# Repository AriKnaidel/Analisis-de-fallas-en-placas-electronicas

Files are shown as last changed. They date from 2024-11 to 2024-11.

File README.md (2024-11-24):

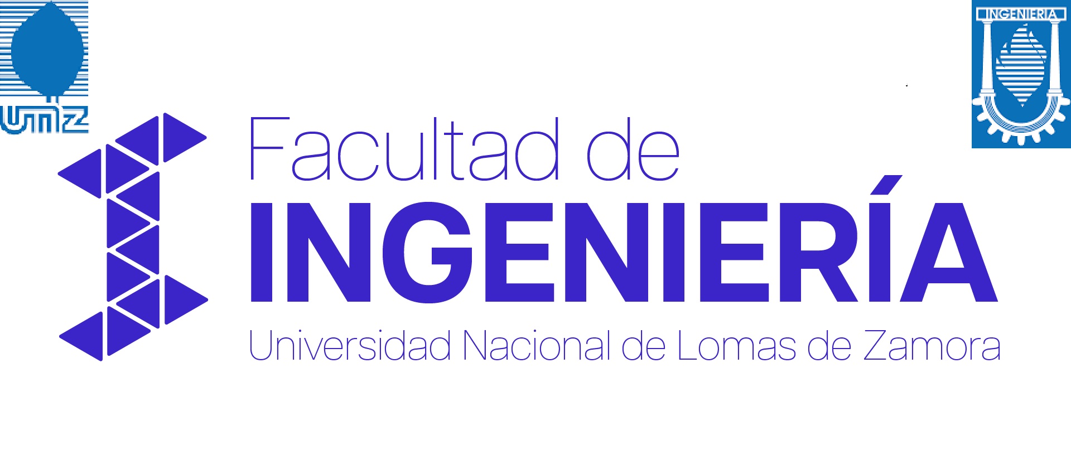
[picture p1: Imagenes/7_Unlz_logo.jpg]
Descripción de la imagen


<h1 align="center">Análisis de fallas en placas electrónicas</h1>

# Detalle del trabajo realizado

El trabajo que realicé es un dispositivo mecatrónico que inspecciona placas electrónicas mediante una cámara y un robot, para luego informar las fallas detectadas. Está pensado para recibir placas electrónicas al final de una línea de producción y verificar que las mismas cuenten con las necesidades mínimas para ser aprobadas, controlando tanto los diferentes elementos electrónicos como los errores de soldadura mediante una cámara y realizando mediciones sobre la placa a través de un robot SCARA. El resultado de estos tres análisis es el que corroborará si placa está o no en condiciones para pasar dicho control de calidad. Todo esto será controlado a través de una interfaz gráfica desarrollada en Python, donde también se podrá observar en tiempo real las diferentes detecciones y mediciones realizadas sobre la placa. 

# Elementos Móviles
El prototipo está formado por tres elementos móviles, y si bien todos se controlan mediante placas electrónicas tipo Arduino estos elementos están integrados mediante un programa de Python para que coordinen sus movimientos y analicen las diferentes placas. Estos elementos son: un robot de tipo SCARA, la base porta placa y un elevador.
# Robot SCARA
El robot SCARA diseñado íntegramente en SOLIDWORKS e impreso con impresora 3D, es de tres grados de libertad (dos giros y un desplazamiento lineal). Este será el encardo de realizar los movimientos necesarios para posicionarse en los puntos de testeo de las placas, y gracias a su efector (puntas de medición) tomará las mediciones correspondientes. Medirá continuidad entre los puntos de testeo de la placa, y se tomarán como válidas las placas que presenten continuidad sobre esos puntos. 

Dicho robot está formado por tres mecanismos móviles (la base, el brazo, regulación de altura) y cada uno cuenta con un motor paso a paso nema 17 que es el encargado de darle el movimiento a cada mecanismo. La base es giratoria y está formada por dos rodamientos axiales de 60mm de diámetro exterior, los cuales acoplan mediante tornillos y tuercas a una polea dentada de 60 dientes, dicha polea acopla a otra polea de 20 dientes a 150mm de distancia ubicada en el eje del motor mediante una correa dentada gt2 de 400mm. De esta base salen tres varillas lisas de 6mm de diámetro y también una varilla roscada de 8mm de diámetro, es en estas varillas donde se acopla el mecanismo del brazo, el cual contiene al brazo 1, al brazo 2 y al efector, este último se encuentra al final del brazo 2. Dicho mecanismo está acoplado a las varillas lisas mediante rodamientos lineales de 6mm de diámetro y a la varilla roscada mediante una tuerca, por lo tanto, este mecanismo gira en concordancia con la base ya que está montado sobre ella. Y como también esta acoplado al mecanismo de regulación de altura cuando la varilla roscada gira, hace que este mecanismo se eleve o baje. El acople entre el motor nema 17 y el brazo 2 es exactamente igual al de la base. En el caso del mecanismo de regulación de altura, el eje del motor está directamente acoplado, mediante un acople flexible a dicha varilla roscada, esta es de 8 mm por vuelta, por lo tanto, cuando este motor gira una vuelta hace que el mecanismo del brazo se eleve o baje 8mm.

Para controlar el robot SCARA se diseñó una placa electrónica mediante el software PROTEUS, luego ese diseño fue impreso en una hoja transfer para transferir las pistas a la placa de cobre y posteriormente se utilizó cloruro férrico para eliminar el cobre y obtener el diseño útil sobre la placa. A dicha placa se le acoplo una esp32, 3 drivers A4988, y borneras para utilizar los pines como entradas o salidas de la esp32. 

<p align="center">
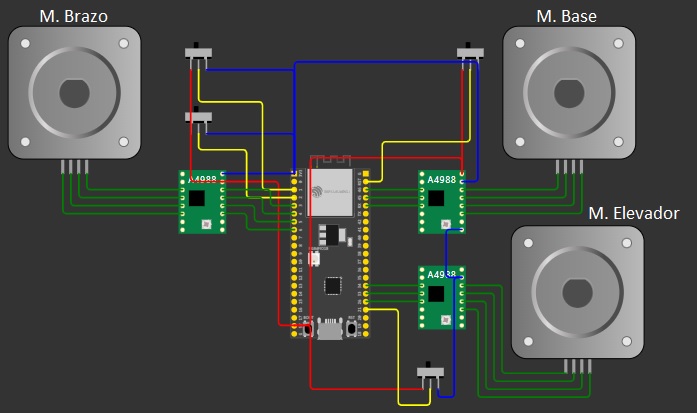
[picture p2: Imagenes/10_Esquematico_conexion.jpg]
Descripción de la imagen
  
</p>
<p align="center"><em>Esquematico conexion robot</em></p>

La esp32 es la encargada de controlar el robot SCARA, esta contiene el código desarrollado en el Arduino IDE, y es capaz de realizar todos los cálculos de la cinemática inversa para que los motores giren la cantidad de grados necesarios y se posicionen en las ubicaciones correctas realizando todos los movimientos al mismo tiempo. Ejecuta la rutina de Home antes de cada movimiento de medición en la placa. Realiza las mediciones de continuidad en dicha placa, gracias al efector del robot. Y también sensa los finales de carrera presentes en el robot para evitar colisiones.

<table>
  <tr>
    <td style="text-align: center;">
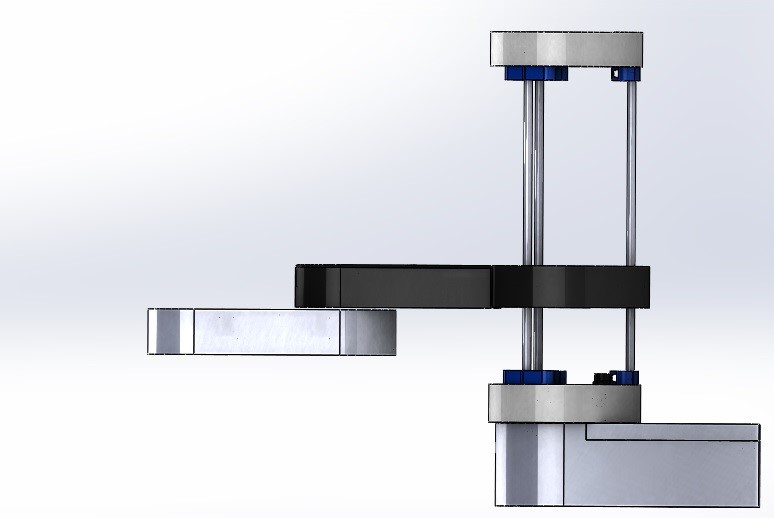
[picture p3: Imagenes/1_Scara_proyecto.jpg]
Descripción de la imagen 1
      
      <p style="text-align: center;"><em>Robot SCARA</em></p>
    </td>
    <td style="text-align: center;">
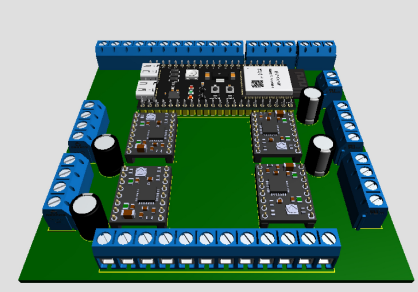
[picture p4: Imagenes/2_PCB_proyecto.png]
Descripción de la imagen 2
      
      <p style="text-align: center;"><em>Controlador Robot SCARA</em></p>
    </td>
  </tr>
</table>

# Cinemática inversa
Con la cinemática inversa, a partir de las coordenadas (x,y) se obtienen los ángulos Ɵ1 y Ɵ2, luego esos ángulos se traducen a pasos para que los motores realicen su trabajo. En el caso del eje que varía la altura se trata de manera separada, es decir no es incluido en los cálculos de cinemática inversa, ya que para el caso de robots de tipo SCARA no es necesario. 

<p align="center">
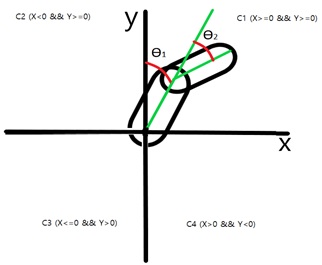
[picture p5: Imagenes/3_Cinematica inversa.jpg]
Descripción de la imagen
  
</p>
<p align="center"><em>Cinemática inversa</em></p>

Para el cálculo de los ángulos Ɵ1 y Ɵ2 se utilizaron las siguientes ecuaciones, y luego se pasó el valor en radianes a grados. 

```cpp
// Calculo de ängulos
tita2R=acos((pow(x,2) +pow(y,2)-pow(L1,2)-pow(L2,2))/((long)2*L1*L2));
tita2G=tita2R*(180/3.1416);
tita1R=atan(x/y) -(atan((L2*sin(tita2R)) /(L1+(L2*cos(tita2R)))));
tita1G=tita1R*(180/3.1416);
```
Las formulas anteriores se obtuvieron mediante el método geométrico, a continuación, el desarrollo:

<p align="center">
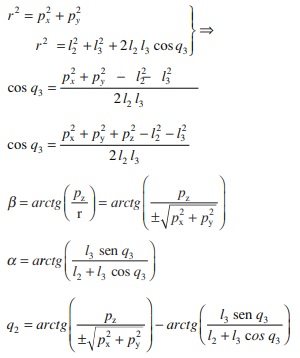
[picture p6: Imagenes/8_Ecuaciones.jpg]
Descripción de la imagen
  
</p>
<p align="center"><em>Metodo geométrico</em></p>

# Base porta placa
En esta base se coloca manualmente la placa a testear. Está formada por 6 elementos impresos en 3D, acoplados al eje de un motor nema 17 que es el encargado de hacerla girar, y un final de carrera óptico que se utiliza para posicionar la placa en el punto óptimo para que la cámara tome la foto para su posterior análisis. Es necesario que la placa gire ya que se analizará tanto el lado de la placa que posee los componentes electrónicos como el lado de las soldaduras.

<p align="center">
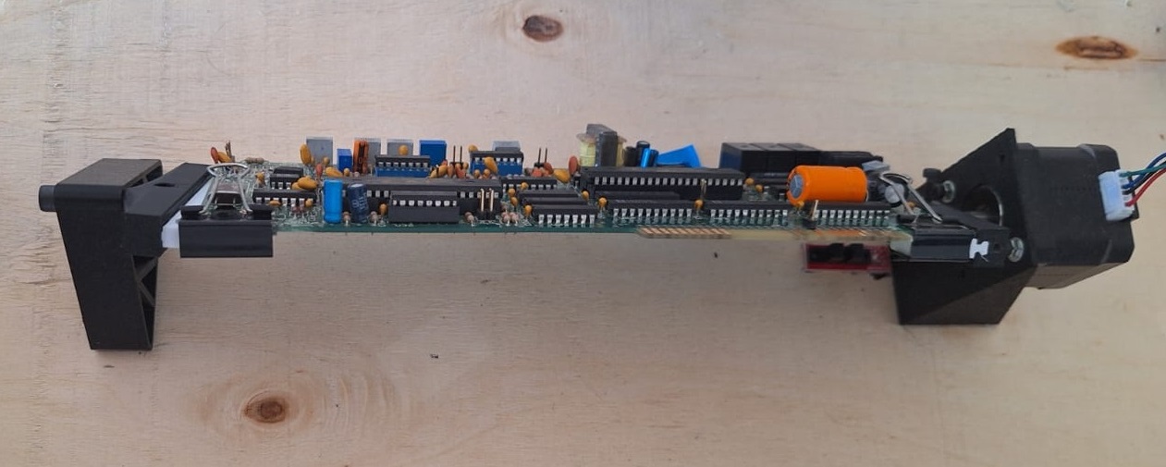
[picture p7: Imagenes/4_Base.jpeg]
Descripción de la imagen
  
</p>
<p align="center"><em>Base porta placa</em></p>

# Elevador
Este dispositivo será el encargado de portar la cámara (utilicé un celular Samsung A54 como cámara) que analizará los componentes electrónicos y las soldaduras de estaño de las placas. Es necesario colocar dicha cámara en este sistema elevador ya que, al realizar la medición con el brazo robótico sobre la placa, este colisionaría con la cámara, por lo tanto, antes de que el robot se posiciones sobre los puntos de testeo de la placa, la cámara es elevada para evitar riesgos de colisión y una vez finalizada la medición del robot y que este vuelve a la posición de seguridad, la cámara baja y se ubica en su posición inicial. 
Este elevador está formado por dos varillas de 6mm de diámetro, y mediante bujes en esas varillas se acopla el carro que contiene la cámara, acoplado a ese carro hay una correa dentada la cual a uno de sus extremos se le acopla un motor nema 17 y en el otro una polea, por lo tanto, al girar el motor la cámara sube o baja. Dicho sistema cuenta también con un final de carrera mecánico que hace que la cámara se posicione a la altura correcta para tomar la foto de la placa para su posterior análisis.

<p align="center">
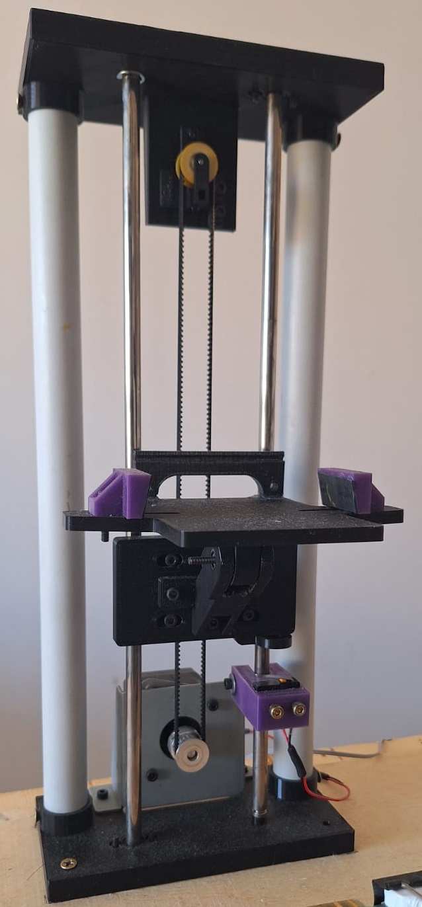
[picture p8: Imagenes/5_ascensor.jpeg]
Descripción de la imagen
  
</p>
<p align="center"><em>Elevador porta cámara</em></p>

Tanto la base porta placa como el elevador están controlados mediante un Arduino Mega 2560. A esta placa se le acopló un Arduino rapms 1.4 para poder controlar los motores paso a paso de cada mecanismo a través de los drivers A4988. El código dentro del Arduino mega fue desarrollado en el Arduino IDE.

<p align="center">
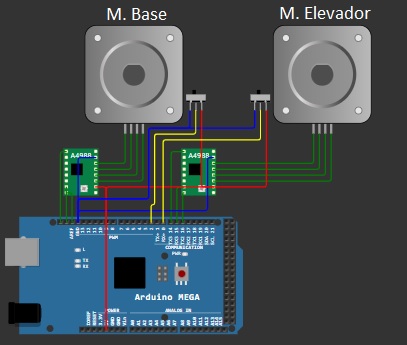
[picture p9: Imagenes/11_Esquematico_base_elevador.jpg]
Descripción de la imagen
  
</p>
<p align="center"><em>Esquematico conexion base y elevador</em></p>

# Integración de los mecanismos
Si bien cada mecanismo nombrado anteriormente (Robot SCARA, base porta placa y el elevador) cuentan con un sistema de control propio, es necesario que actúen de manera sincronizada. Para esto se desarrolló una aplicación con PYTHON, la cual hace que cada mecanismo se sincronice y actúe en el momento adecuado para lograr de manera efectiva el testeo de las diferentes placas electrónicas. Dicha aplicación se ejecutará en una computadora y tanto el controlador del robot (esp32), como el controlador de la base y el elevador (Arduino Mega) se conectarán a la computadora mediante los puertos seriales, la aplicación será la encargada de enviar y recibir las diferentes señales tanto a la esp32 como al Arduino para que los mecanismos realicen los movimientos correspondientes. También esta aplicación será la encargada de recibir las imágenes que toma la cámara y procesarlas para detectar los faltantes de los componentes electrónicos o errores en la soldadura. Antes de realizar la detección en las placas es necesario etiquetar lo que el sistema tiene que detectar, esto lo hice tomando fotos de cada componente individualmente y de las soldaduras erróneas y luego cargándolo al código de la aplicación. Para la captura de imágenes utilicé la aplicación IRIUM, instalada tanto en el celular como en la computadora, ambos dispositivos deben estar conectados a la misma red wifi. De esta manera, y con la ayuda de la librería “Open cv” se pueden realizar capturas de video o imágenes para su posterior análisis. 

Se detallan las librerias utilizadas en el codigo python, donde se realizo la integracion de los dispositivos moviles y la interfaz gráfica.
```python
import cv2
import numpy as np
import serial
import time
#Interfaz grafica
import sys
import threading
from PyQt5.QtWidgets import QApplication, QWidget, QPushButton, QLabel, QHBoxLayout, QVBoxLayout, QSpacerItem, QSizePolicy, QFrame
from PyQt5.QtCore import Qt, QTimer
from PyQt5.QtGui import QPixmap, QImage
```
A continuacion se detallan fragmentos del codigo en python, donde muestran los comnados utilizados para establecer la comunicacion serial entre el Arduino Mega y la ESP32.
```python
#Comunicacion con el arduino Mega (Base porta placa y elevador)
arduino = serial.Serial('COM5', 9600)
#Comunicacion con la ESP32 (Robot SCARA)
time.sleep(2)  # Espera un poco para la inicialización del Arduino
esp32 = serial.Serial('COM3', 9600)
time.sleep(2)

def send_command(command):
    """Envía un comando al Arduino y espera la respuesta."""
    arduino.write(command.encode())  # Enviar el comando
    time.sleep(0.2)  # Breve espera para la transmisión

def send_com_esp(command):
    """Envía un comando a la ESP32 y espera la respuesta."""
    esp32.write(command.encode())  # Enviar el comando
    time.sleep(0.1)

    while True:
        if esp32.in_waiting > 0:  # Verifica si hay datos disponibles
            respuesta = esp32.readline().decode('utf-8').strip()  # Lee y decodifica la respuesta
            return respuesta  # Retorna la respuesta
    return "No se recibió respuesta de la ESP32"

```
# Descripción del proceso de análisis de las placas
El proceso de análisis de la placa comienza una vez que se presiona el botón “Siguiente” de la aplicación desarrollada con python, previamente se debe colocar una placa en la base porta placa. Luego de presionar el botón dicha base girará hasta actuar el final de carrera óptico para luego ubicarse en la posición de enfoque correcta de la cámara, con los componentes electrónicos hacia la cámara, luego el elevador bajará la cámara hasta actuar el final de carrera, es en ese momento que esta toma una foto de los componentes de la placa electrónica, como la cámara y la computadora están ejecutando al mismo tiempo la aplicación IRIUM es que se transfiera dicha foto a la computadora para su análisis. En base a la foto tomada se realiza un reconocimiento de los componentes presentes, marcando cada uno en la imagen tomada, y en caso que existan faltantes estos serán listados en la interfaz gráfica. 

Finalizado este análisis, pasa automáticamente a analizase el otro lado de la placa, es decir las soldaduras, por lo tanto, la base porta placa gira 180º y la cámara toma una foto de este lado, el procedimiento en este caso es el mismo que para los componentes, recuadrando cada error de soldadura e informando la cantidad detectada. Lo que resta es la medición de continuidad en la placa, realizada por el robot gracias a su efector, ya finalizada la detección de errores de soldadura, el elevador que es quien porta la cámara, la subirá para dar lugar al robot a posicionarse sobre la placa y evitar colisiones. 

El primer movimiento que realiza el robot es ubicarse en su posición de home una vez que la cámara se encuentra en la posición segura en el extremo superior del elevador, finalizado el home, el robot se mueve a la posición de medición, donde el efector entrará en contacto con los puntos de testeo de la placa y realizará la medición de continuidad, mostrando en la interfaz gráfica el resultado. Cuando esta medición finaliza, el robot vuelve a su posición de home y la base porta placa se ubica en la posición inicial lista para realizar el cambio de placa. Una vez finalizado el proceso sabemos que componentes electrónicos faltan, cuantos errores de soldadura posee la placa y si la medición de continuidad, la cual simula la medición de un fusible, es la correcta. Al colocar otra placa y presionar el botón “Siguiente” de la interfaz gráfica el proceso comienza nuevamente.

# Costos 
A continuación, muestro los diferentes elementos que componen al proyecto junto con su costo de adquisición. Hay que tener en cuenta que hubo costos extra debido principalmente a componentes electrónicos que se quemaron. Esos costos extra rondan los 30 usd.

<p align="center">
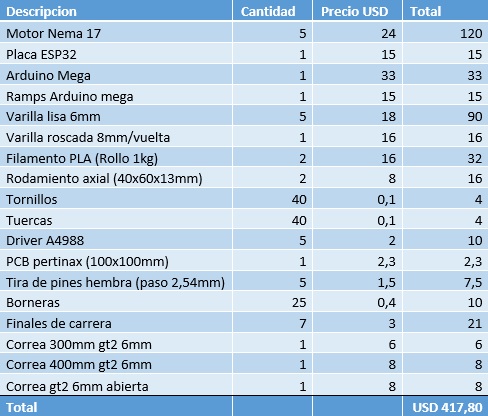
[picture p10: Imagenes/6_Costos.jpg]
Descripción de la imagen
  
</p>
<p align="center"><em>Costos</em></p>

# Conclusiones

El desarrollo de este dispositivo fue un desafío tanto técnico como personal, enfrentándome a diferentes obstáculos que requirieron de creatividad y perseverancia para ser superados. Cada etapa del proyecto planteo problemas únicos, como el diseño y la impresión 3D, la calibración de los motores, el desarrollo de código tanto en Python como Arduino, la calibración de la cámara para el análisis de imágenes. 

Uno de los mayores desafíos fue el manejo del tiempo, ya que el proyecto implicó coordinar diferentes tareas independientes entre sí, como el diseño del robot, el desarrollo electrónico, la programación, entre otras tareas. El proyecto duró 3 veces más de lo planificado, principalmente debido a diferentes componentes electrónicos que se fueron dañando a lo largo del proyecto, a diferentes tecnologías que tuve que aprender a utilizar para poder aplicarlas de manera eficiente y a la limitación de tiempo debido a mis responsabilidades laborales. Esto representó un gran desafío, ya que debía equilibrar mi trabajo con el avance del proyecto.

También voy a destacar que fue necesario enfrentar limitaciones de recursos, optimizando el uso de materiales y herramientas disponibles, y recurrir a soluciones creativas para problemas inesperados, como la adaptación de un celular como cámara o la fabricación artesanal de la placa electrónica de control del robot SCARA.

El proyecto no solo logró cumplir con los objetivos planteados, sino que también se convirtió en una valiosa experiencia de aprendizaje de 653hs, abarcando áreas fundamentales como la robótica, la electrónica y la programación. Estos conocimientos son esenciales para el desarrollo profesional de un ingeniero, y este proyecto me permitió consolidar esas habilidades clave y profundizar en la integración de las mismas.

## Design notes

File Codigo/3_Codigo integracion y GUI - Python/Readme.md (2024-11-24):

El Archivo (1_opencvvideo_Rev2.6.py) es donde se encuentra el codigo que integra al robot SCARA (controlado por la esp32) y a la basa-elevador (controlado por un Arduino mega). Este codigo envia y recibe comandos a traves de los puertos seriales y es asi como sincroniza los movimientos de los dispositivos, a demas contiene la interfaz grafica donde se puede ver en tiempo real las detecciones y mediciones que realiza, tambien se lo controla. 

Tanto el codigo (1_opencvvideo_Rev2.6.py) como las imagenes presentes deben estar ubicados en la misma carpeta, ya que este recurre a las imagenes para realizar las diferentes detecciones.

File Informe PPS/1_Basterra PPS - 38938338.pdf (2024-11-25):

______________________________________________________________________________

# Informe de Práctica Profesional Supervisada

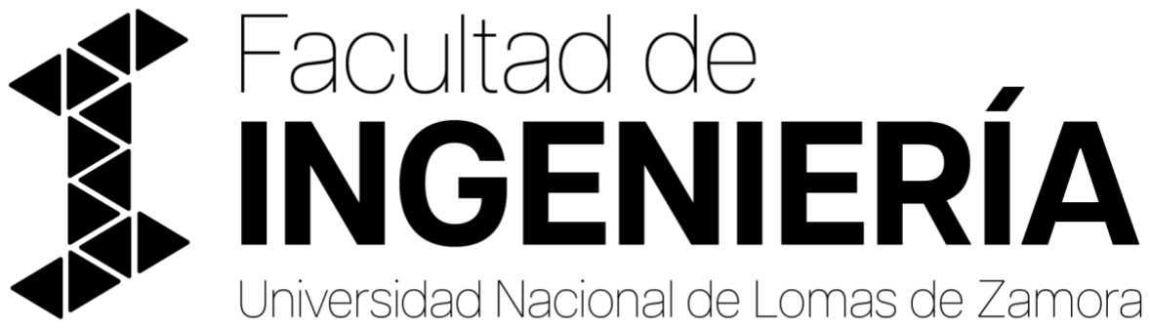
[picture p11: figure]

Institución: UNLZ-FI

Tutor Institucional: Cristian Lukaszewicz

Tutor académico: Cristian Lukaszewicz

Cargo institucional: Docente, materia: Proyecto final en ing. mecatrónica

DNI: 37.936.857

_ _ _ _ _ _ _ _ _ _ _ _ _ _ _ _

Firma del Tutor Institucional

______________________________________________________________________________

Índice

______________________________________________________________________________
Reservado a la facultad para evaluación

______________________________________________________________________________
Lugar donde he realizado la PPS

Desarrollé mi Práctica Profesional Supervisada, en el laboratorio de mecatrónica de la Universidad Nacional de Lomas de Zamora, Facultad de Ingeniería (UNLZ-FI), ubicada en Camino de Cintura, Av. Juan XXIII, Lomas de Zamora, Provincia de Buenos Aires.

Este laboratorio está equipado con diversas herramientas y tecnologías que facilitaron el desarrollo del proyecto, como fuentes de alimentación regulables, osciloscopios, multímetros, y equipos de medición avanzada. También cuenta con un espacio de trabajo adecuado para el montaje y prueba de prototipos en electrónica y mecatrónica. Además, tuve la oportunidad de recibir asesoramiento continuo de los docentes Cristian Lukaszewicz y Ezequiel Blanca, quienes me orientaron en temas específicos relacionados principalmente con inteligencia artificial y electrónica, permitiéndome profundizar en los aspectos técnicos y metodológicos del proyecto.

______________________________________________________________________________
Detalle del trabajo realizado

El trabajo que realicé es un dispositivo mecatrónico que inspecciona placas electrónicas mediante una cámara y un robot, para luego informar las fallas detectadas. Está pensado para recibir placas electrónicas al final de una línea de producción y verificar que las mismas cuenten con las necesidades mínimas para ser aprobadas, controlando tanto los diferentes elementos electrónicos como los errores de soldadura mediante una cámara y realizando mediciones sobre la placa a través de un robot SCARA. El resultado de estos tres análisis es el que corroborará si placa está o no en condiciones para pasar dicho control de calidad. Todo esto será controlado a través de una interfaz gráfica desarrollada en Python, donde también se podrá observar en tiempo real las diferentes detecciones y mediciones realizadas sobre la placa.

Elementos Móviles
El prototipo está formado por tres elementos móviles, y si bien todos se controlan mediante placas electrónicas tipo Arduino estos elementos están integrados mediante un programa de Python para que coordinen sus movimientos y analicen las diferentes placas. Estos elementos son: un robot de tipo SCARA, la base porta placa y un elevador.

Robot SCARA
El robot SCARA diseñado íntegramente en SOLIDWORKS e impreso con impresora 3D, es de tres grados de libertad (dos giros y un desplazamiento lineal). Este será el encardo de realizar los movimientos necesarios para posicionarse en los puntos de testeo de las placas, y gracias a su efector (puntas de medición) tomará las mediciones correspondientes. Medirá continuidad entre los puntos de testeo de la placa, y se tomarán como válidas las placas que presenten continuidad sobre esos puntos.

Dicho robot está formado por tres mecanismos móviles (la base, el brazo, regulación de altura) y cada uno cuenta con un motor paso a paso nema 17 que es el encargado de darle el movimiento a cada mecanismo. La base es giratoria y está formada por dos rodamientos axiales de 60mm de diámetro exterior, los cuales acoplan mediante tornillos y tuercas a una polea dentada de 60 dientes, dicha polea acopla a otra polea de 20 dientes a 150mm de distancia ubicada en el eje del motor mediante una correa dentada gt2 de 400mm. De esta base salen tres varillas lisas de 6mm de diámetro y también una varilla roscada de 8mm de diámetro, es en estas varillas donde se acopla el mecanismo del brazo, el cual contiene al brazo 1, al brazo 2 y al efector, este último se encuentra al final del brazo 2. Dicho mecanismo está acoplado a las varillas lisas mediante rodamientos lineales de 6mm de diámetro y a la varilla roscada mediante una tuerca, por lo tanto, este mecanismo gira en concordancia con la base ya que está montado

______________________________________________________________________________

sobre ella. Y como también esta acoplado al mecanismo de regulación de altura cuando la varilla roscada gira, hace que este mecanismo se eleve o baje. El acople entre el motor nema 17 y el brazo 2 es exactamente igual al de la base. En el caso del mecanismo de regulación de altura, el eje del motor está directamente acoplado, mediante un acople flexible a dicha varilla roscada, esta es de 8 mm por vuelta, por lo tanto, cuando este motor gira una vuelta hace que el mecanismo del brazo se eleve o baje 8mm.

Para controlar el robot SCARA se diseñó una placa electrónica mediante el software PROTEUS, luego ese diseño fue impreso en una hoja transfer para transferir las pistas a la placa de cobre y posteriormente se utilizó cloruro férrico para eliminar el cobre y obtener el diseño útil sobre la placa. A dicha placa se le acoplo una esp32, 3 drivers A4988, y borneras para utilizar los pines como entradas o salidas de la esp32.

La esp32 es la encargada de controlar el robot SCARA, esta contiene el código desarrollado en el Arduino IDE, y es capaz de realizar todos los cálculos de la cinemática inversa para que los motores giren la cantidad de grados necesarios y se posicionen en las ubicaciones correctas realizando todos los movimientos al mismo tiempo. Ejecuta la rutina de Home antes de cada movimiento de medición en la placa. Realiza las mediciones de continuidad en dicha placa, gracias al efector del robot. Y también sensa los finales de carrera presentes en el robot para evitar colisiones.

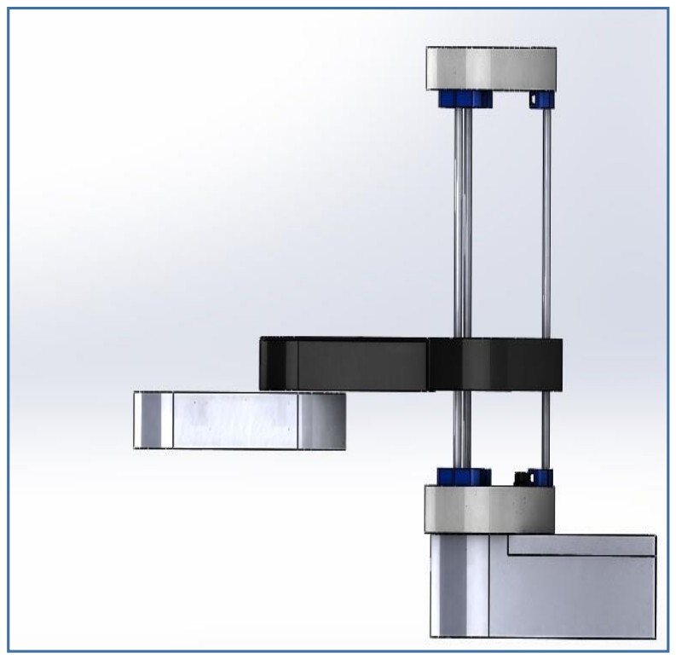
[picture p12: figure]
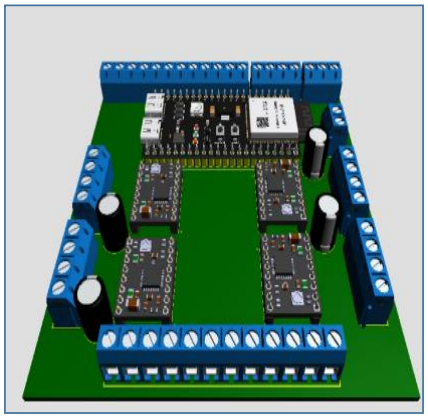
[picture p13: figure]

Cinemática Inversa 1.Robot SCARA (vista lateral) | 2.Controlador Robot SCARA

______________________________________________________________________________
Cinemática inversa
Con la cinemática inversa, a partir de las coordenadas (x,y) se obtienen los ángulos ti1 y ti2, luego esos ángulos se traducen a pasos para que los motores realicen su trabajo. En el caso del eje que varía la altura se trata de manera separada, es decir no es incluido en los cálculos de cinemática inversa, ya que para el caso de robots de tipo SCARA no es necesario.

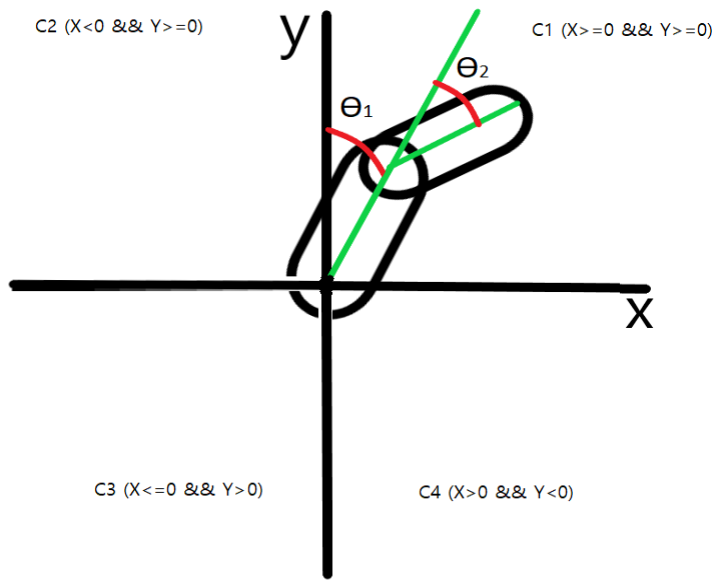
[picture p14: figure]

3.Cinemática inversa

Para el cálculo de los ángulos ti1 y ti2 se utilizaron las siguientes ecuaciones, y luego se pasó el valor en radianes a grados.

tita2R=acos((pow(x,2) +pow(y,2)-pow(L1,2)-pow(L2,2))/((long)2*L1*L2)); tita2G=tita2R*(180/3.1416);
tita1R=atan(x/y) -(atan((L2*sin(tita2R)) /(L1+(L2*cos(tita2R))))); tita1G=tita1R*(180/3.1416);

Las formulas anteriores se obtuvieron mediante el método geométrico, a continuación, el desarrollo:

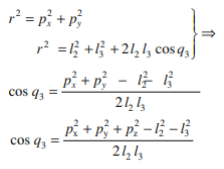
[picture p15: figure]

______________________________________________________________________________

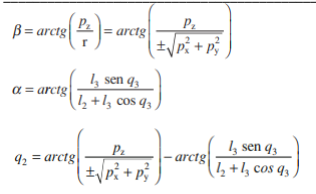
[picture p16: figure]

Base porta placa
En esta base se coloca manualmente la placa a testear. Está formada por 6 elementos impresos en 3D, acoplados al eje de un motor nema 17 que es el encargado de hacerla girar, y un final de carrera óptico que se utiliza para posicionar la placa en el punto óptimo para que la cámara tome la foto para su posterior análisis. Es necesario que la placa gire ya que se analizará tanto el lado de la placa que posee los componentes electrónicos como el lado de las soldaduras.

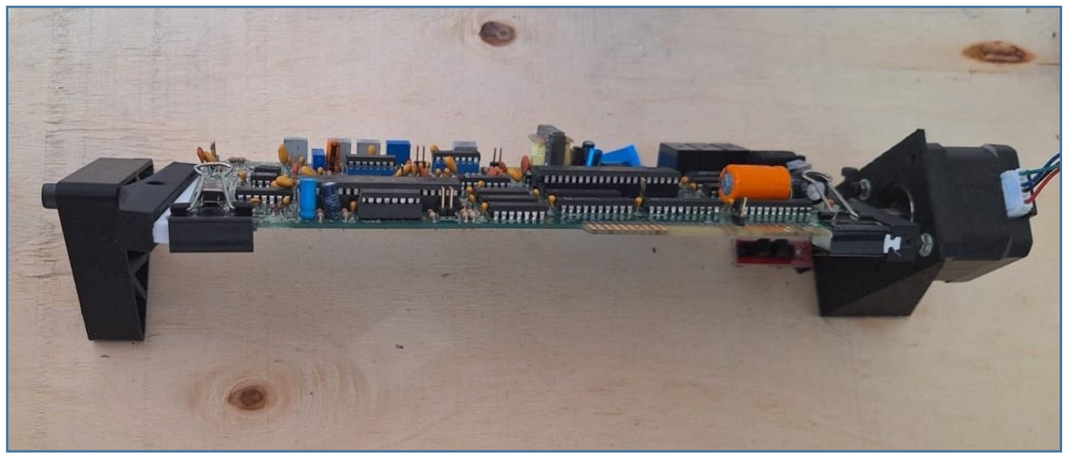
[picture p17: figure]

Elevador
Este dispositivo será el encargado de portar la cámara (utilicé un celular Samsung A54 como cámara) que analizará los componentes electrónicos y las soldaduras de estaño de las placas. Es necesario colocar dicha cámara en este sistema elevador ya que, al realizar la medición con el brazo robótico sobre la placa, este colisionaría con la cámara, por lo tanto, antes de que el robot se posiciones sobre los puntos de testeo de la placa, la cámara es elevada para evitar riesgos de

4.Base porta placa

______________________________________________________________________________

colisión y una vez finalizada la medición del robot y que este vuelve a la posición de seguridad, la cámara baja y se ubica en su posición inicial.

Este elevador está formado por dos varillas de 6mm de diámetro, y mediante bujes en esas varillas se acopla el carro que contiene la cámara, acoplado a ese carro hay una correa dentada la cual a uno de sus extremos se le acopla un motor nema 17 y en el otro una polea, por lo tanto, al girar el motor la cámara sube o baja. Dicho sistema cuenta también con un final de carrera mecánico que hace que la cámara se posicione a la altura correcta para tomar la foto de la placa para su posterior análisis.

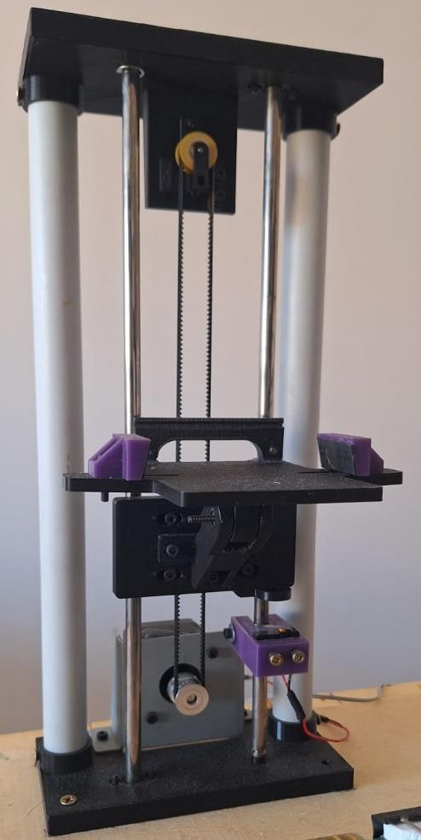
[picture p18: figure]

Tanto la base porta placa como el elevador están controlados mediante un Arduino Mega 2560. A esta placa se le acopló un Arduino rapms 1.4 para poder controlar los motores paso a paso de cada mecanismo a través de los drivers A4988. El código dentro del Arduino mega fue desarrollado en el Arduino IDE.

5.Elevador porta cámara

______________________________________________________________________________

Integración de los mecanismos
Si bien cada mecanismo nombrado anteriormente (Robot SCARA, base porta placa y el elevador) cuentan con un sistema de control propio, es necesario que actúen de manera sincronizada. Para esto se desarrolló una aplicación con PYTHON, la cual hace que cada mecanismo se sincronice y actúe en el momento adecuado para lograr de manera efectiva el testeo de las diferentes placas electrónicas. Dicha aplicación se ejecutará en una computadora y tanto el controlador del robot (esp32), como el controlador de la base y el elevador (Arduino Mega) se conectarán a la computadora mediante los puertos seriales, la aplicación será la encargada de enviar y recibir las diferentes señales tanto a la esp32 como al Arduino para que los mecanismos realicen los movimientos correspondientes. También esta aplicación será la encargada de recibir las imágenes que toma la cámara y procesarlas para detectar los faltantes de los componentes electrónicos o errores en la soldadura. Antes de realizar la detección en las placas es necesario etiquetar lo que el sistema tiene que detectar, esto lo hice tomando fotos de cada componente individualmente y de las soldaduras erróneas y luego cargándolo al código de la aplicación. Para la captura de imágenes utilicé la aplicación IRIUM, instalada tanto en el celular como en la computadora, ambos dispositivos deben estar conectados a la misma red wifi. De esta manera, y con la ayuda de la librería “Open cv” se pueden realizar capturas de video o imágenes para su posterior análisis.

Descripción del proceso de análisis de las placas
El proceso de análisis de la placa comienza una vez que se presiona el botón “Siguiente” de la aplicación desarrollada con python, previamente se debe colocar una placa en la base porta placa. Luego de presionar el botón dicha base girará hasta actuar el final de carrera óptico para luego ubicarse en la posición de enfoque correcta de la cámara, con los componentes electrónicos hacia la cámara, luego el elevador bajará la cámara hasta actuar el final de carrera, es en ese momento que esta toma una foto de los componentes de la placa electrónica, como la cámara y la computadora están ejecutando al mismo tiempo la aplicación IRIUM es que se transfiera dicha foto a la computadora para su análisis. En base a la foto tomada se realiza un reconocimiento de los componentes presentes, marcando cada uno en la imagen tomada, y en caso que existan faltantes estos serán listados en la interfaz gráfica. Finalizado este análisis, pasa
automáticamente a analizase el otro lado de la placa, es decir las soldaduras, por lo tanto, la base porta placa gira 180º y la cámara toma una foto de este lado, el procedimiento en este caso es el mismo que para los componentes, recuadrando cada error de soldadura e informando la cantidad detectada. Lo que resta es la

______________________________________________________________________________

medición de continuidad en la placa, realizada por el robot gracias a su efector, ya finalizada la detección de errores de soldadura, el elevador que es quien porta la cámara, la subirá para dar lugar al robot a posicionarse sobre la placa y evitar colisiones. El primer movimiento que realiza el robot es ubicarse en su posición de home una vez que la cámara se encuentra en la posición segura en el extremo superior del elevador, finalizado el home, el robot se mueve a la posición de medición, donde el efector entrará en contacto con los puntos de testeo de la placa y realizará la medición de continuidad, mostrando en la interfaz gráfica el resultado. Cuando esta medición finaliza, el robot vuelve a su posición de home y la base porta placa se ubica en la posición inicial lista para realizar el cambio de placa. Una vez finalizado el proceso sabemos que componentes electrónicos faltan, cuantos errores de soldadura posee la placa y si la medición de continuidad, la cual simula la medición de un fusible, es la correcta. Al colocar otra placa y presionar el botón “Siguiente” de la interfaz gráfica el proceso comienza nuevamente.

Costos
A continuación, muestro los diferentes elementos que componen al proyecto junto con su costo de adquisición. Hay que tener en cuenta que hubo costos extra debido principalmente a componentes electrónicos que se quemaron. Esos costos extra rondan los 30 usd.

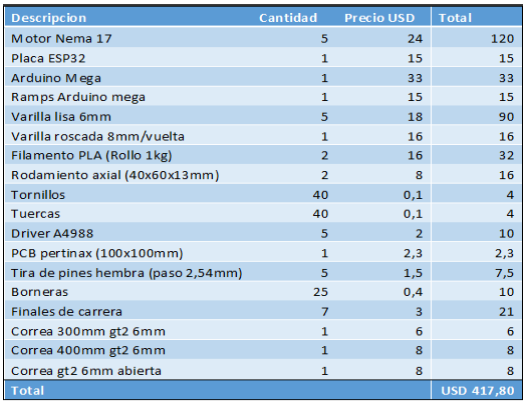
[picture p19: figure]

6.Costos

______________________________________________________________________________

Conclusiones

El desarrollo de este dispositivo fue un desafío tanto técnico como personal, enfrentándome a diferentes obstáculos que requirieron de creatividad y perseverancia para ser superados. Cada etapa del proyecto planteo problemas únicos, como el diseño y la impresión 3D, la calibración de los motores, el desarrollo de código tanto en Python como Arduino, la calibración de la cámara para el análisis de imágenes.

Uno de los mayores desafíos fue el manejo del tiempo, ya que el proyecto implicó coordinar diferentes tareas independientes entre sí, como el diseño del robot, el desarrollo electrónico, la programación, entre otras tareas. El proyecto duró 3 veces más de lo planificado, principalmente debido a diferentes componentes electrónicos que se fueron dañando a lo largo del proyecto, a diferentes tecnologías que tuve que aprender a utilizar para poder aplicarlas de manera eficiente y a la limitación de tiempo debido a mis responsabilidades laborales. Esto representó un gran desafío, ya que debía equilibrar mi trabajo con el avance del proyecto.

También voy a destacar que fue necesario enfrentar limitaciones de recursos, optimizando el uso de materiales y herramientas disponibles, y recurrir a soluciones creativas para problemas inesperados, como la adaptación de un celular como cámara o la fabricación artesanal de la placa electrónica de control del robot SCARA.

El proyecto no solo logró cumplir con los objetivos planteados, sino que también se convirtió en una valiosa experiencia de aprendizaje de 653hs, abarcando áreas fundamentales como la robótica, la electrónica y la programación. Estos conocimientos son esenciales para el desarrollo profesional de un ingeniero, y este proyecto me permitió consolidar esas habilidades clave y profundizar en la integración de las mismas.

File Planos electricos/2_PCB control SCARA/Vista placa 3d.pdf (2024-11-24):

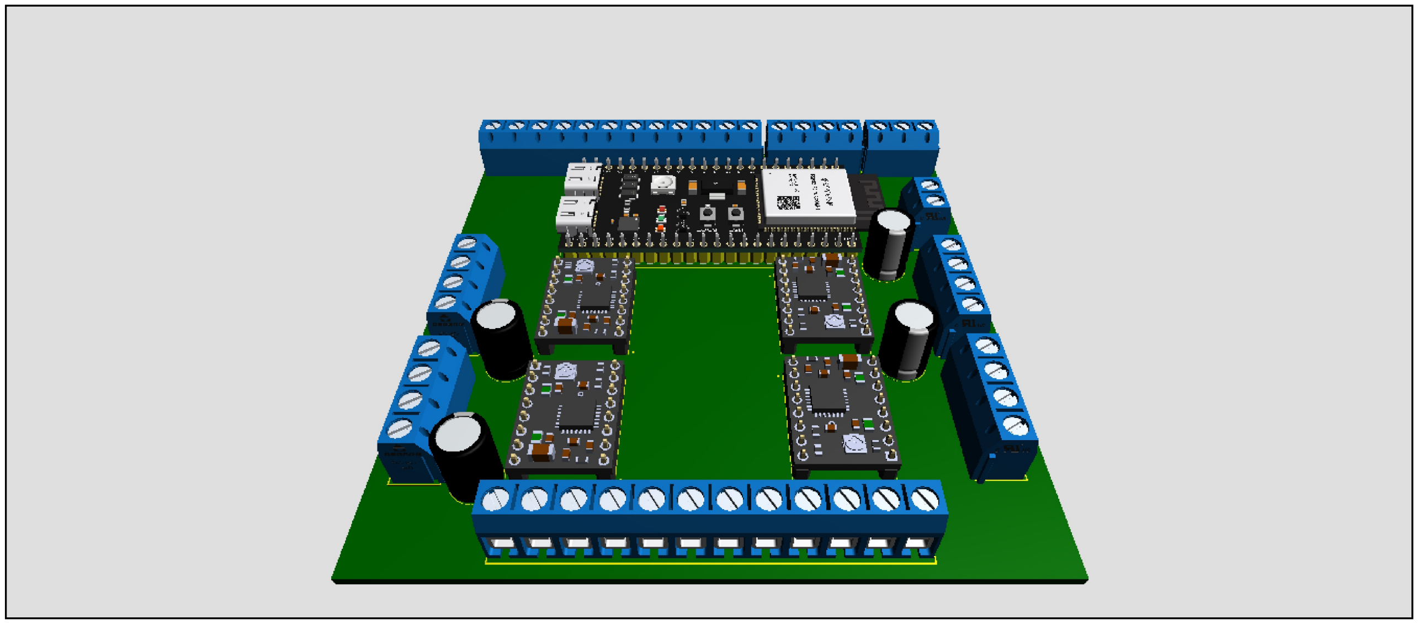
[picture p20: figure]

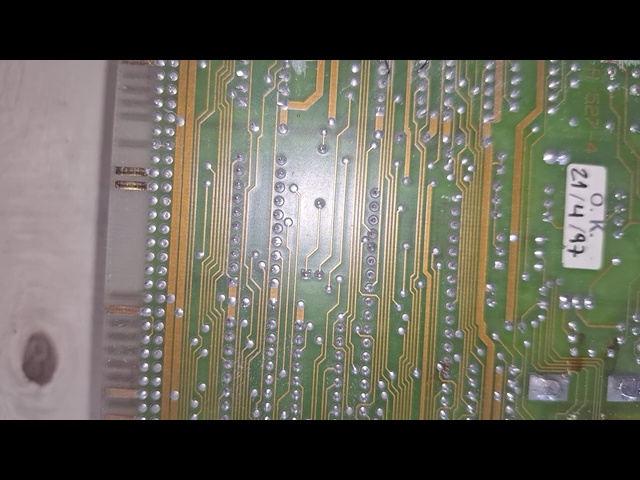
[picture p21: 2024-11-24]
Codigo/3_Codigo integracion y GUI - Python/imsold.jpg

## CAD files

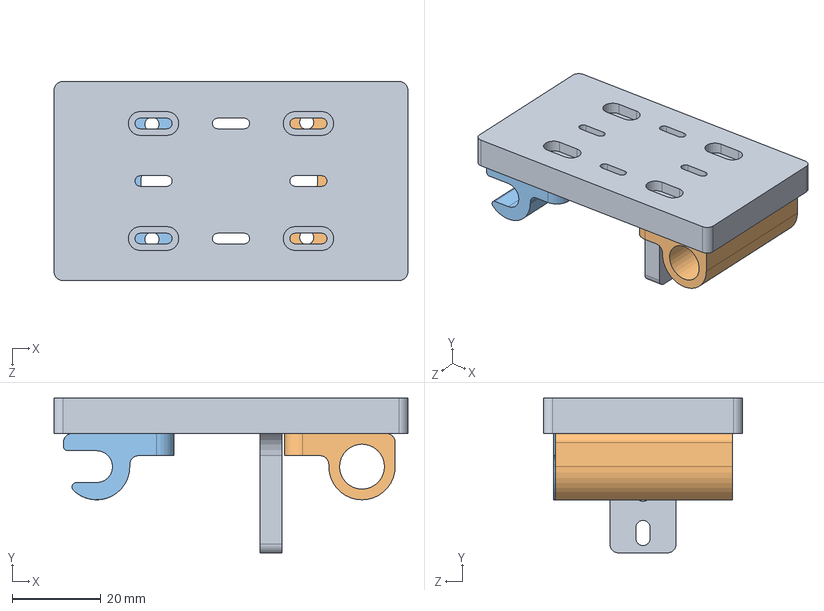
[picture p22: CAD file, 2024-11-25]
Diseño 3D/3_Elevador/Ensamblaje2.SLDASM
80.0 x 35.0 x 45.0 mm
CarroBase
GuiaConBuje
GuiaSinBuje

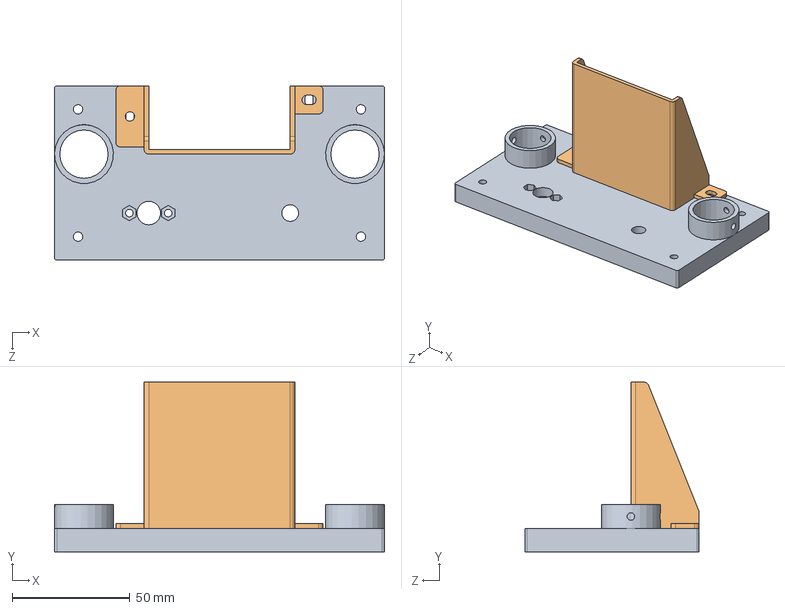
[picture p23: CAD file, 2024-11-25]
Diseño 3D/3_Elevador/Ensamblaje1.SLDASM
140.0 x 72.0 x 74.0 mm
Base
soporteMotor

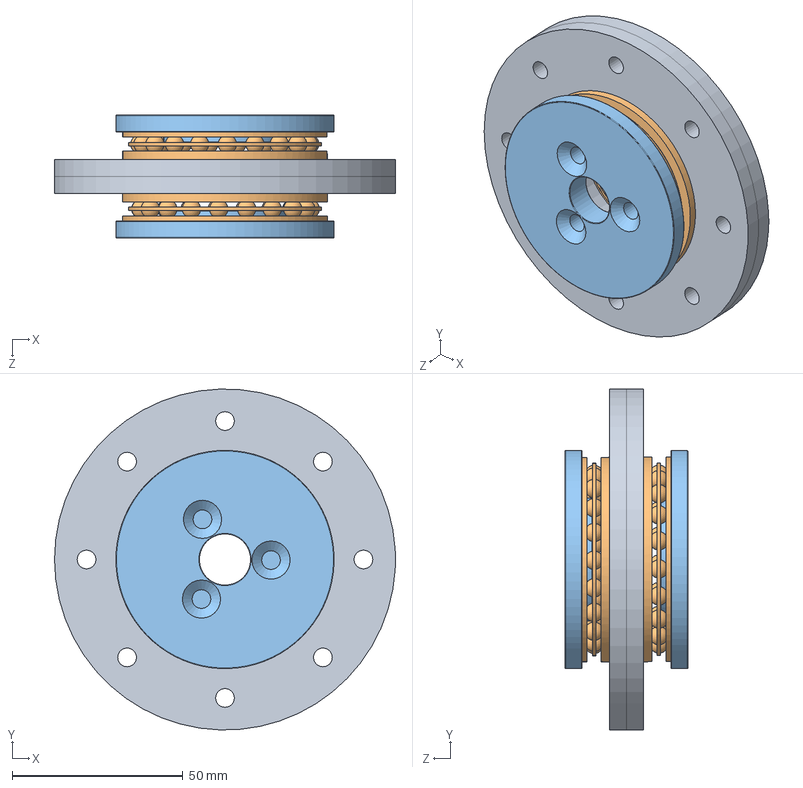
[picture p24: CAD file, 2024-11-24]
Diseño 3D/2_Robot Scara/Ensamblaje1.SLDASM
100.0 x 100.0 x 36.0 mm
4_Apoya rod rev2 x 2
single direction thrust ball bearing_ks x 2
3_sujeta_rod_sup rev2 x 2

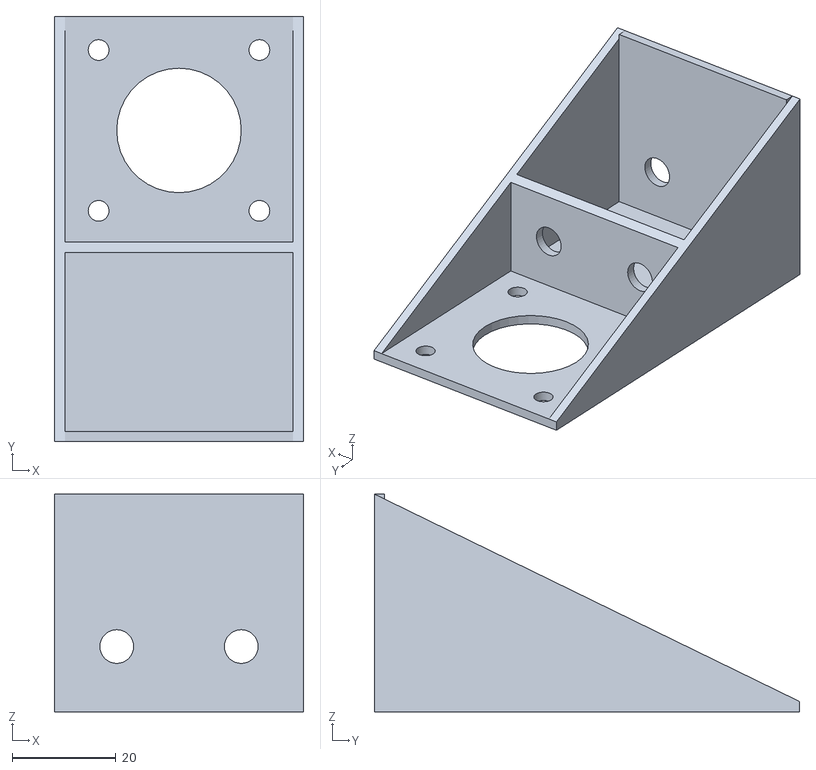
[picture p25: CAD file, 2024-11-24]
Diseño 3D/1_Base porta placa/soporte motor placa.STL
48.0 x 82.0 x 42.0

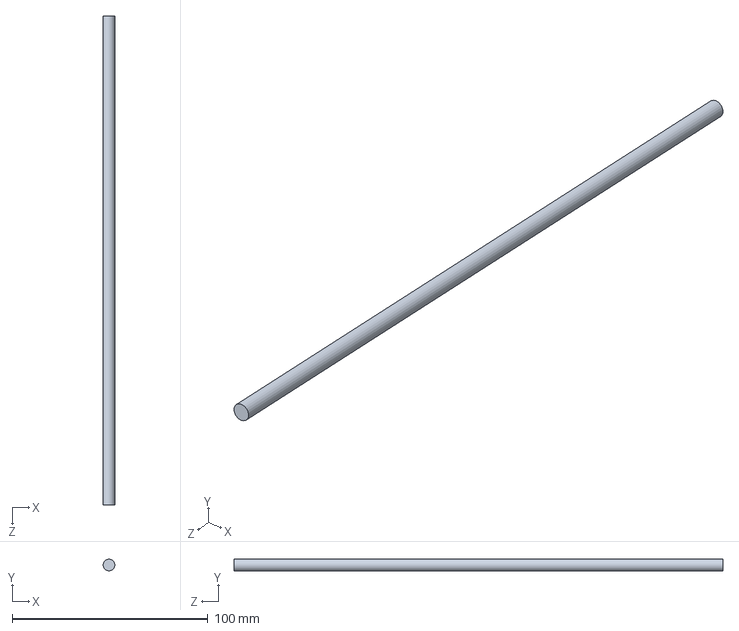
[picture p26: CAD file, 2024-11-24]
Diseño 3D/2_Robot Scara/18_Varilla altura.SLDPRT
6.00 x 6.00 x 250.0 mm

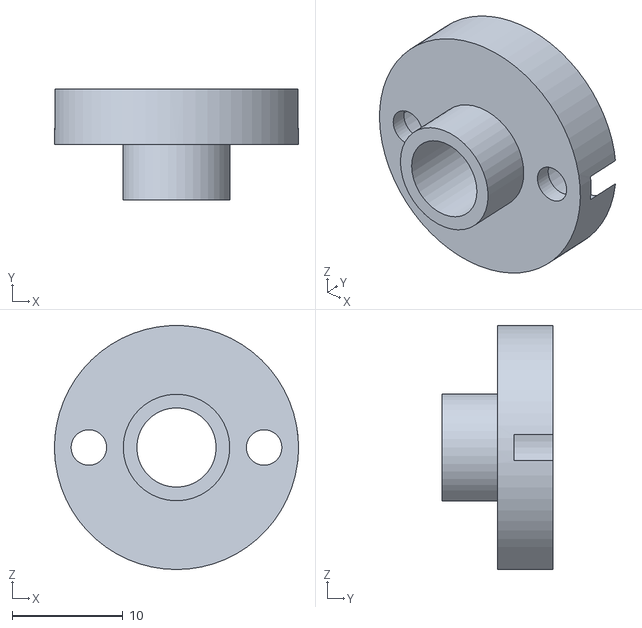
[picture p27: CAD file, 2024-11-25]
Diseño 3D/3_Elevador/AcopleVarillaTOP.STL
22.0 x 10.0 x 22.0

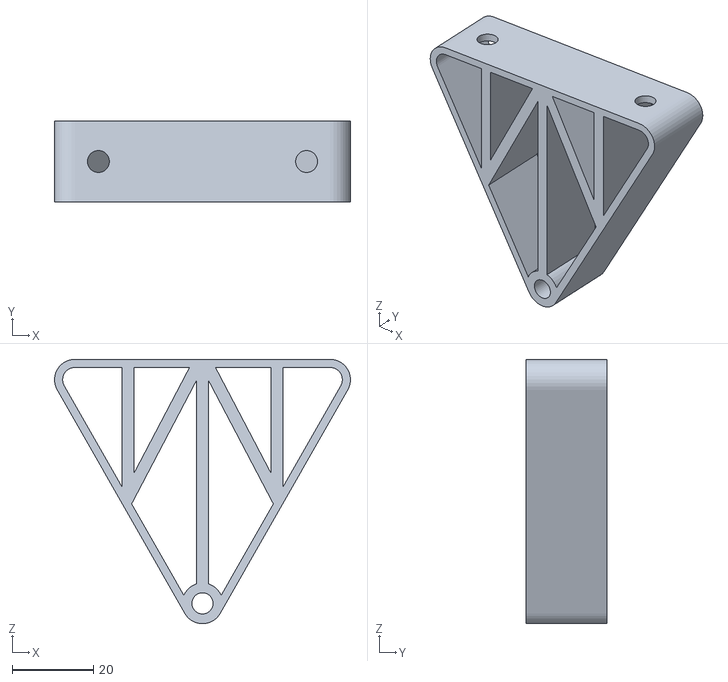
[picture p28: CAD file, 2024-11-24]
Diseño 3D/1_Base porta placa/soporte placa otro lado.STL
72.8 x 20.0 x 65.0

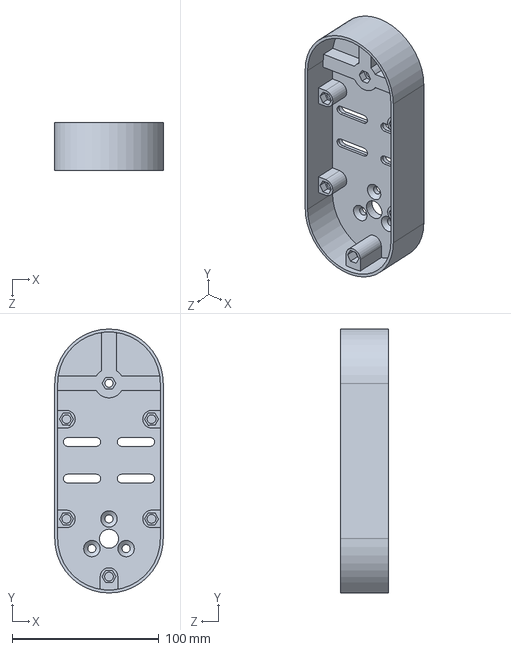
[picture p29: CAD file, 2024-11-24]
Diseño 3D/2_Robot Scara/19_Ultimo brazo.SLDPRT
74.0 x 180.0 x 32.8 mm

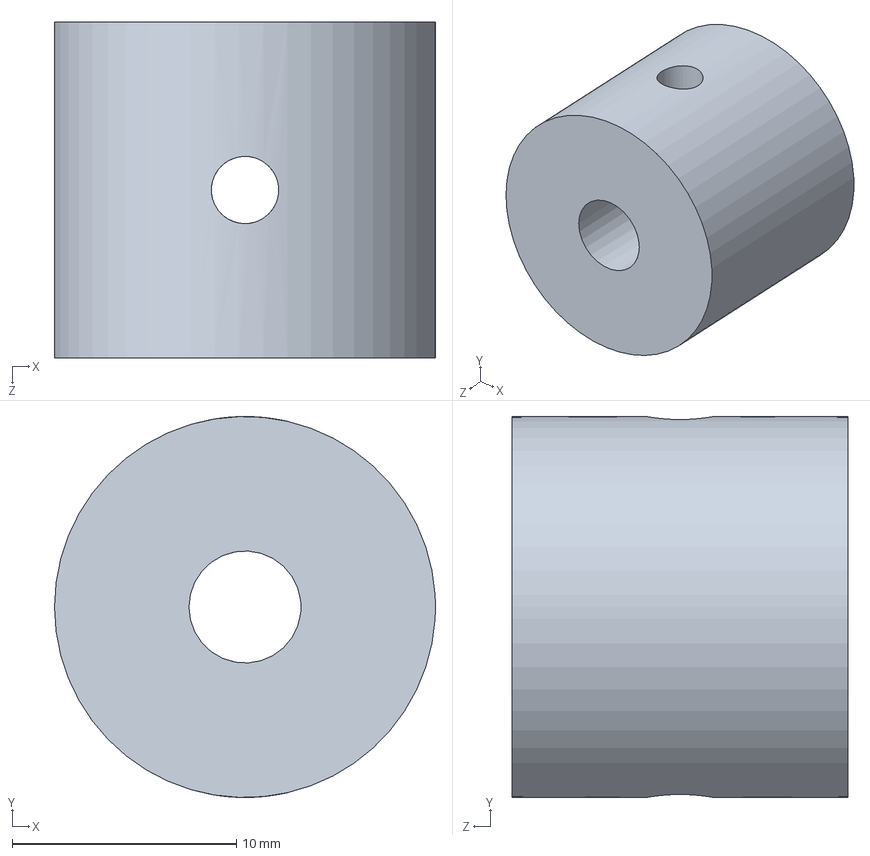
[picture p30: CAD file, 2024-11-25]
Diseño 3D/3_Elevador/TapoTuerca.SLDPRT
17.0 x 17.0 x 15.0 mm

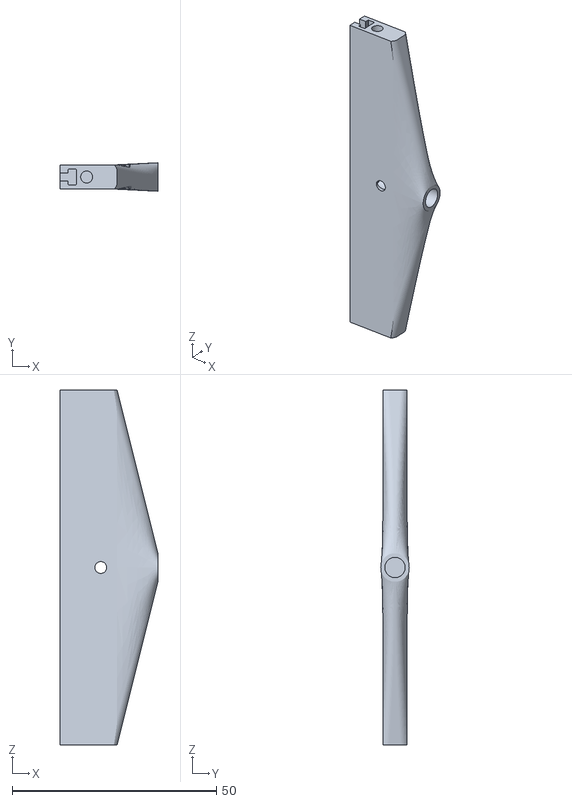
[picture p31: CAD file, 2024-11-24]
Diseño 3D/1_Base porta placa/2_Sostenpcb_Motor.STL
24.0 x 7.00 x 87.0

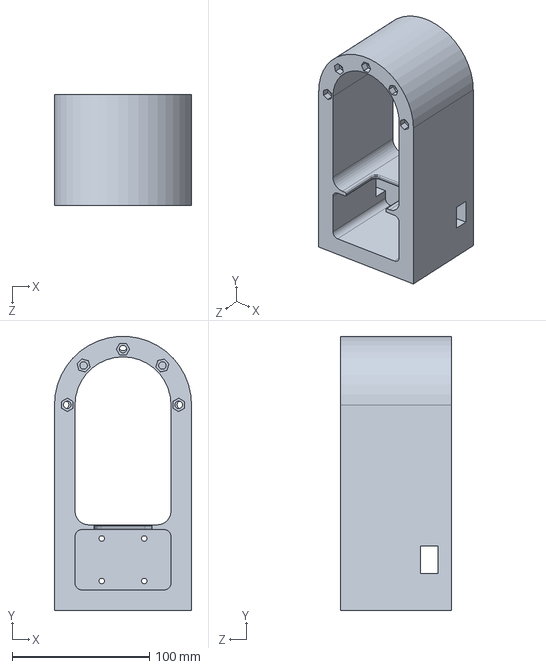
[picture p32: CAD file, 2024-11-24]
Diseño 3D/2_Robot Scara/22_Base final.SLDPRT
100.0 x 199.9 x 81.0 mm

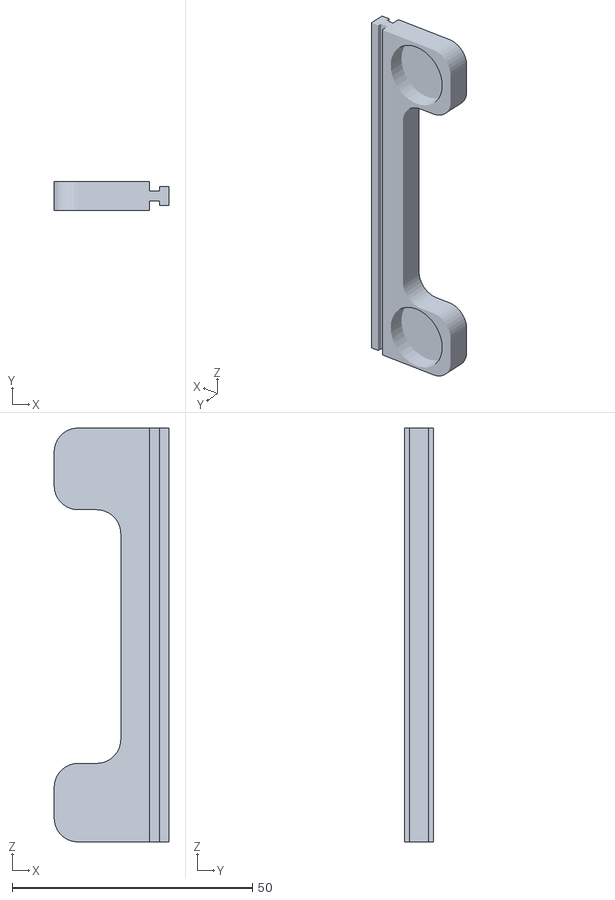
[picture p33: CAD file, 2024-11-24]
Diseño 3D/1_Base porta placa/1_Sostenpcb_rev1.1.STL
23.9 x 6.00 x 86.1

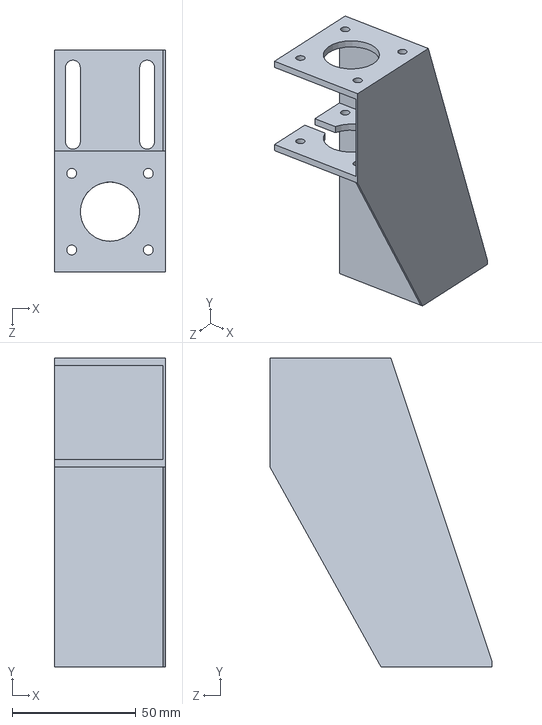
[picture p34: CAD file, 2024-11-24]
Diseño 3D/2_Robot Scara/15_Soporte motor 2b.SLDPRT
45.0 x 125.0 x 90.0 mm

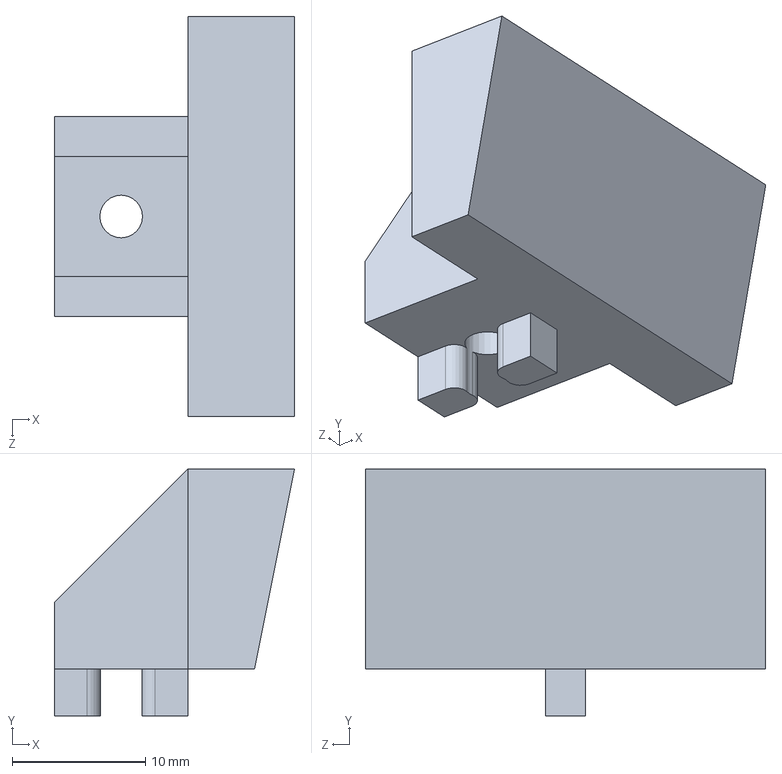
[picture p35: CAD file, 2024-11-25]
Diseño 3D/3_Elevador/TrabaCam.SLDPRT
18.0 x 18.5 x 30.0 mm

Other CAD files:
Diseño 3D/3_Elevador/AcopleVarilla.SLDPRT
Diseño 3D/2_Robot Scara/60T-gt2-6mm-5mm-dshaft-pressfit.stl
Diseño 3D/3_Elevador/PortaFinalDeCarrera.SLDPRT
Diseño 3D/2_Robot Scara/23_base final rev1.SLDPRT
Diseño 3D/2_Robot Scara/10_Espaciador rueda dentada.SLDPRT
Diseño 3D/2_Robot Scara/10_Espaciador rueda dentada.STL
Diseño 3D/2_Robot Scara/11_Sosten varilla.SLDPRT
Diseño 3D/2_Robot Scara/11_Sosten varilla.STL
Diseño 3D/2_Robot Scara/12_Soporte parado.SLDPRT
Diseño 3D/2_Robot Scara/12_Soporte parado.STL
Diseño 3D/2_Robot Scara/13_Buje varilla roscada.SLDPRT
Diseño 3D/2_Robot Scara/13_Buje varilla roscada.STL
Diseño 3D/2_Robot Scara/14_Soporte motor 2.SLDPRT
Diseño 3D/2_Robot Scara/14_Soporte motor 2.STL
Diseño 3D/2_Robot Scara/15_Soporte motor 2b.STL
Diseño 3D/2_Robot Scara/16_Carro.SLDPRT
Diseño 3D/2_Robot Scara/16_Carro.STL
Diseño 3D/2_Robot Scara/17_Brazo carro - copia.SLDPRT
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

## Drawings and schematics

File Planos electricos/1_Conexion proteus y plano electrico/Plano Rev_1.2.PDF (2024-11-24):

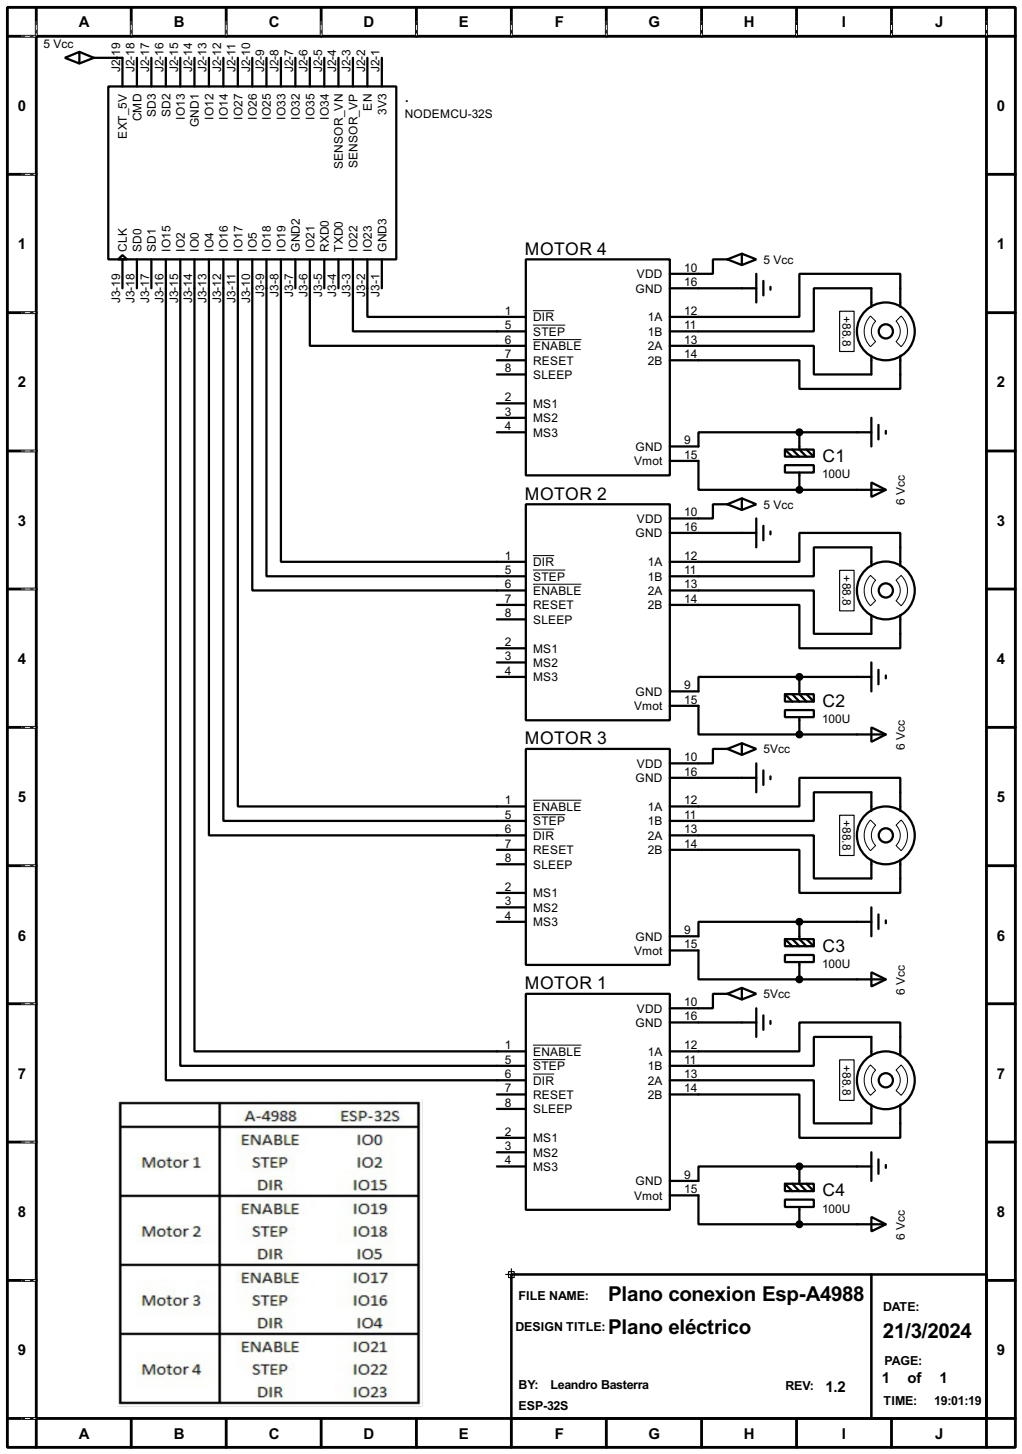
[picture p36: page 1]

12
11

FILE NAME:
DESIGN TITLE:Plano eléctrico

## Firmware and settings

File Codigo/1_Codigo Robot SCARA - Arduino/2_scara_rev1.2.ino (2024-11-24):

#include <cmath>
char input;
int sum_angulos = 1;
float cont1 = 0.0;
float cont2 = 0.0;
float cont3 = 0.0;
float X;
float Y;
float Z;
float x;
float y;
float Zpaso;
int val_menu;
int m;
String mensaje1 = "Coordenada X: ";
String mensaje2 = "Coordenada Y: ";
String mensajez = "Coordenada Z: ";
String mensaje3 = "Coordenada X Ingresada: ";
String mensaje4 = "Coordenada Y Ingresada: ";
String mensajez_ing = "Coordenada Z Ingresada: ";
String mensaje5 = "Menu: ";
String mensaje6 = "1_Cinematica inversa: ";
String mensaje7 = "2_HOME: ";
const int led = 13;
const int L1 = 160;
const int L2 = 106;
float tita2R;
float tita2G;
float tita1R;
float tita1G;
float tita1G_a_pasos;
float tita2G_a_pasos;
float tita1G_actual;
float tita1pasos_anterior = 0;
float tita2G_actual;
float tita2pasos_anterior = 0;
float z_pasos_anterior = 0;
float z_actual;
int C = 0;
float temp = 2;
float temp_base;
float temp_brazo;
float temp_varilla;
float cont_base = 0.0;
float cont_brazo = 0.0;
float cont_varilla = 0.0;
float paso_max;
float rel_base;
float rel_brazo;
float rel_varilla;
float cont_prueba = 0.0;
long ti;
long par1T2;
long par2T2;
float par3T2;
float par4T2;
float par1T1;
float par2T1;
float par4T22;
float angeje1;
int movehome = 0;
int cine = 0;
//Finales de carrera
#define fcb1 34
volatile bool homeb1 = false;
#define fcb2 26
volatile bool homeb2 = false;
#define fc_brazo_1 27  //35
#define fc_brazo_2 32
volatile bool pararmotorbrazo35 = false;
volatile bool pararmotorbrazo32 = false;
#define fc_zsuperior 33
#define fc_zinferior 25
volatile bool pararmotorz_sup = false;
volatile bool pararmotorz_inf = false;
//Puntas
#define puntas 14
int estadopuntas = 0;

//Declaracion de motores
// Motor 1
#define step 2
#define dir 15
#define temp 2
#define EN 0
// Motor 2 Brazo 2
#define step_2 18
#define dir_2 5
#define EN_2 19
// Motor 3 Base
#define step_3 16
#define dir_3 4
#define EN_3 17
// Motor 4
#define step_4 22
#define dir_4 23
#define EN_4 21
void angulos(float x, float y, float Z) {
  do {
    if (isnan(tita1G) || isnan(tita2G)) {
      Serial.println("Posicion X o Y fuera del alcance");
      Serial.println("");
      Serial.println("Vuelva a ingreasar las coordenadas ");
    }
    //Serial.println(mensaje1);
    //while(Serial.available()==0){

    //}
    //x=Serial.parseInt();
    //limpiarBufferSerial();
    //Serial.print(mensaje3);
    //Serial.println(x);

    Serial.println(mensaje2);
    //while(Serial.available()==0){

    //}
    //y=Serial.parseInt();
    //limpiarBufferSerial();
    //Serial.print(mensaje4);
    //Serial.println(y);
    do {
      if (Z > 102) {
        Serial.println("Coordenada Z fuera de rango ");
        Serial.println(" ");
        Serial.println("Ingresela nuevamente");
      }
      if (Z < 0) {
        Serial.println("Ingrese un valor positivo de Z ");
        Serial.println(" ");
        Serial.println("Ingreselo nuevamente");
      }
      //Serial.println(mensajez);
      //while(Serial.available()==0){

      //}
      //Z=Serial.parseInt();
      //limpiarBufferSerial();
      //Serial.print(mensajez_ing);
      //Serial.println(Z);

      z_actual = Z * (1600 / 8);  //1600 porque esta configurado con micropasos 1/8, 8 porque son 8mm por vuelta de la varilla roscada
      Zpaso = z_actual - z_pasos_anterior;
      if (Zpaso < 0) {
        Zpaso = -1 * Zpaso;
        digitalWrite(dir_4, LOW);  //Low baja
      }
      //Serial.println("Cantidad de pasos Varilla: ");
      //Serial.println(Zpaso);
    } while (Z > 102);  // si Z es mayor a 150mm o negativo hay que ingresarlo nuevamente
    tita2R = acos((pow(x, 2) + pow(y, 2) - pow(L1, 2) - pow(L2, 2)) / ((long)2 * L1 * L2));
    tita2G = tita2R * (180 / 3.1416);  //paso de radianes a grados
    tita1R = atan(x / y) - (atan((L2 * sin(tita2R)) / (L1 + (L2 * cos(tita2R)))));
    tita1G = tita1R * (180 / 3.1416);

  } while (isnan(tita1G) || isnan(tita2G));
  movehome = 1;
  /*tita2R=acos((pow(x,2)+pow(y,2)-pow(L1,2)-pow(L2,2))/((long)2*L1*L2));
  tita2G=tita2R*(180/3.1416);
  tita1R=atan(x/y)-(atan((L2*sin(tita2R))/(L1+(L2*cos(tita2R)))));
  tita1G=tita1R*(180/3.1416);*/
  //return(tita2G,tita1G);
  //Primer cuadrante
  if (x >= 0 && y >= 0) {
    Serial.println("Ambos numeros son positivos, primer cuadrante");
    tita1G = 90 - tita1G;
    C = 1;
  }
  //Segundo cuadrante
  if (x < 0 && y >= 0) {
    Serial.println("X negativo, Y positivo, segundo cuadrante");
    tita1G = 90 - tita1G;
    C = 2;
  }
  //Tercer cuadrante
  if (x <= 0 && y < 0) {
    Serial.println("Ambos numeros son negativos, tercer cuadrante");
    tita1G = 270 - tita1G;
    C = 3;
  }
  //Cuarto cuadrante
  if (x > 0 && y < 0) {
    Serial.println("X positivo, Y negativo, Cuarto cuadrante");
    tita1G = -90 - tita1G;
    C = 4;
  }
  /* MODIFICACION POSICIONAMIENTO SOBRE EJES
  if (x >= 0 && y > 0) {
        Serial.println("Ambos numeros son positivos, primer cuadrante");
        tita1G=90-tita1G;
        C=1;
      }
  //Segundo cuadrante
  if (x < 0 && y > 0) {
        Serial.println("X negativo, Y positivo, segundo cuadrante");
        tita1G=90-tita1G;
        C=2;
      }
  //Tercer cuadrante
  if (x < 0 && y < 0) {
        Serial.println("Ambos numeros son negativos, tercer cuadrante");
        tita1G=270-tita1G;
        C=3;
      }
    //Cuarto cuadrante
  if (x > 0 && y < 0) {
        Serial.println("X positivo, Y negativo, Cuarto cuadrante");
        tita1G=-90-tita1G;
        C=4;
      }*/
}
void limpiarBufferSerial() {
  while (Serial.available() > 0) {
    char c = Serial.read();  // Lee y descarta los caracteres restantes.
  }
}
void girar(float paso_max, float tita1G_a_pasos, float tita2G_a_pasos, float Zpaso, float temp_base, float temp_brazo, float temp_varilla) {
  cont_base = 0.0;
  cont_brazo = 0.0;
  cont_varilla = 0.0;
  float ratio_base = (float)tita1G_a_pasos / paso_max;
  float ratio_brazo = (float)tita2G_a_pasos / paso_max;
  float ratio_varilla = (float)Zpaso / paso_max;
  cont_prueba = 0.0;
  int cont_prueba2 = 0;
  while (cont_base < tita1G_a_pasos || cont_brazo < tita2G_a_pasos || cont_varilla < Zpaso) {
    //if (pararmotorbase){
    //digitalWrite(EN_3, HIGH);
    //Serial.println("Final de carrera de la base activado");
    //digitalWrite(EN_3, LOW);
    //}
    if (pararmotorbrazo35 || pararmotorbrazo32) {
      digitalWrite(EN_2, HIGH);
    }
    if (pararmotorz_sup || pararmotorz_inf) {
      digitalWrite(EN_4, HIGH);
    }
    cont_prueba++;
    if (((cont_base < tita1G_a_pasos) && (cont_base / cont_prueba < ratio_base)) || paso_max / tita1G_a_pasos == 1.0) {  //((cont_base / (float) tita1G_a_pasos) < ratio_base * cont_varilla)) {
      digitalWrite(step_3, HIGH);
      delayMicroseconds(700);
      digitalWrite(step_3, LOW);
      cont_base++;
    }

    if (((cont_brazo < tita2G_a_pasos) && (cont_brazo / cont_prueba < ratio_brazo)) || paso_max / tita2G_a_pasos == 1.0) {  //((cont_brazo / (float) tita2G_a_pasos) < ratio_brazo * cont_varilla)) {
      digitalWrite(step_2, HIGH);
      delayMicroseconds(700);
      digitalWrite(step_2, LOW);
      cont_brazo++;
    }

    if (((cont_varilla < Zpaso) && (cont_varilla / cont_prueba < ratio_varilla)) || paso_max / Zpaso == 1.0) {
      digitalWrite(step_4, HIGH);
      delayMicroseconds(700);
      digitalWrite(step_4, LOW);
      cont_varilla++;
    } /* Pruebo si el motor 2 termina al mismo momento que los demas motores, (-262,9,30)
    if(cont_brazo==560){
      cont_prueba2++;
      //Serial.println("Motor brazo termino 2222222: ");
      //cont_brazo=0.0;
    }
    if(cont_prueba2==1){
      cont_prueba2++;
      Serial.println("Motor brazo termino 2222222: ");
      //cont_brazo=0.0;
    }*/

    // Ajustar pausas para sincronizar
    delayMicroseconds(500);  // Puedes ajustar este valor para sincronizar más finamente
  }
}
/*void gira_base(float tita1G_a_pasos,float temp_base){////////////// funcion gira base
  for(float pasos_base_M3=0.0; pasos_base_M3<tita1G_a_pasos; pasos_base_M3++){
    cont_base++;
    cont_brazo++;
    cont_varilla++;
    //digitalWrite(step, HIGH);
    digitalWrite(step_3, HIGH);
    //digitalWrite(step_2, HIGH);
    //digitalWrite(step_4, HIGH);
    delay(temp_base);
    //digitalWrite(step,LOW);
    digitalWrite(step_3,LOW);
    //digitalWrite(step_2,LOW);
    //digitalWrite(step_4,LOW);
    delay(temp_base);
    return;
  }
}*/
void home_base() {
  delay(500);
  digitalWrite(dir_3, LOW);  // con LOW gira AntiHorario
  while (homeb1 == false && homeb2 == false) {
    digitalWrite(step_3, HIGH);
    delayMicroseconds(700);
    digitalWrite(step_3, LOW);
    delayMicroseconds(700);
  }
  delay(500);
  //Serial.println("Salio del While");
  if (homeb1) {
    digitalWrite(dir_3, HIGH);
    for (int i = 0; i < 2200; i++) {
      digitalWrite(step_3, HIGH);
      delayMicroseconds(700);
      digitalWrite(step_3, LOW);
      delayMicroseconds(700);
    }
  }
  /*if(homeb2){
    digitalWrite(dir_3,HIGH);
    for(int i=0;i < 4000; i++){
      digitalWrite(step_3, HIGH);
      delayMicroseconds(700);
      digitalWrite(step_3, LOW);
      delayMicroseconds(700);
    }
  }*/
  //homeb1=false;
  //homeb2=false;
}
void home_brazo() {
  delay(500);
  digitalWrite(dir_2, HIGH);  // con HIGH gira Horario
  while (pararmotorbrazo35 == false && pararmotorbrazo32 == false) {
    digitalWrite(step_2, HIGH);
    delayMicroseconds(700);
    digitalWrite(step_2, LOW);
    delayMicroseconds(700);
  }
  delay(500);
  //Serial.println("Salio del While");
  if (pararmotorbrazo35) {
    digitalWrite(dir_2, LOW);
    for (int i = 0; i < 3650; i++) {
      digitalWrite(step_2, HIGH);
      delayMicroseconds(700);
      digitalWrite(step_2, LOW);
      delayMicroseconds(700);
    }
  }
  if (pararmotorbrazo32) {
    digitalWrite(dir_2, HIGH);
    for (int i = 0; i < 3650; i++) {
      digitalWrite(step_2, HIGH);
      delayMicroseconds(700);
      digitalWrite(step_2, LOW);
      delayMicroseconds(700);
    }
  }
  //pararmotorbrazo35=false;
  //pararmotorbrazo32=false;
}
void home_z() {
  digitalWrite(dir_4, HIGH);  // con LOW baja
  while (pararmotorz_sup == false) {
    digitalWrite(step_4, HIGH);
    delayMicroseconds(700);
    digitalWrite(step_4, LOW);
    delayMicroseconds(700);
  }
  delay(500);
  //Serial.println("Salio del While");
  if (pararmotorz_sup) {
    digitalWrite(dir_4, LOW);
    for (int i = 0; i < 2000; i++) {  //21100
      digitalWrite(step_4, HIGH);
      delayMicroseconds(700);
      digitalWrite(step_4, LOW);
      delayMicroseconds(700);
    }
  }
  //pararmotorz_sup=false;
  //pararmotorz_inf=false;
}

void IRAM_ATTR f1() {
  homeb1 = true;
}
void IRAM_ATTR f2() {
  homeb2 = true;
}
void IRAM_ATTR finalpararbrazo35() {
  pararmotorbrazo35 = true;
}
void IRAM_ATTR finalpararbrazo32() {
  pararmotorbrazo32 = true;
}
void IRAM_ATTR finalpararz_sup() {
  pararmotorz_sup = true;
}
void IRAM_ATTR finalpararz_inf() {
  pararmotorz_inf = true;
}
void setup() {
  Serial.begin(9600);
  //Inicio Motores
  //Motor 1
  pinMode(step, OUTPUT);
  pinMode(dir, OUTPUT);
  pinMode(EN, OUTPUT);
  //Motor 2
  pinMode(step_2, OUTPUT);
  pinMode(dir_2, OUTPUT);
  pinMode(EN_2, OUTPUT);
  //Motor 3
  pinMode(step_3, OUTPUT);
  pinMode(dir_3, OUTPUT);
  pinMode(EN_3, OUTPUT);
  //Motor 4
  pinMode(step_4, OUTPUT);
  pinMode(dir_4, OUTPUT);
  pinMode(EN_4, OUTPUT);
  //Fin motores
  //Finales carrera
  pinMode(fcb1, INPUT_PULLUP);
  attachInterrupt(digitalPinToInterrupt(fcb1), f1, FALLING);
  pinMode(fcb2, INPUT_PULLUP);
  attachInterrupt(digitalPinToInterrupt(fcb2), f2, FALLING);
  pinMode(fc_brazo_1, INPUT_PULLUP);
  attachInterrupt(digitalPinToInterrupt(fc_brazo_1), finalpararbrazo35, CHANGE);
  pinMode(fc_brazo_2, INPUT_PULLUP);
  attachInterrupt(digitalPinToInterrupt(fc_brazo_2), finalpararbrazo32, CHANGE);
  pinMode(fc_zsuperior, INPUT_PULLUP);
  attachInterrupt(digitalPinToInterrupt(fc_zsuperior), finalpararz_sup, CHANGE);
  pinMode(fc_zinferior, INPUT_PULLUP);
  attachInterrupt(digitalPinToInterrupt(fc_zinferior), finalpararz_inf, CHANGE);
  pinMode(puntas, INPUT_PULLUP);
}

void loop() {

  if (Serial.available()) {
    char input = Serial.read();
  
  //Serial.println(input);
  //val_menu=Serial.parseInt();
  //limpiarBufferSerial();
  if (input == 'm') {
    //Serial.println("Proceso de medicion");
    estadopuntas = digitalRead(puntas);

    // Envía el estado del pulsador por el puerto serial
    if (estadopuntas == LOW) {
      Serial.println("Continuidad");
    } else {
      Serial.println("No continuidad");
    }

    // Espera 500 ms antes de leer el estado del pulsador nuevamente
    delay(500);
  }
  if (input == 'h') {
    Serial.println("Rutina de Home");
    Serial.println("Homeb1:");
    Serial.println(homeb1);
    Serial.println("Homeb12:");
    Serial.println(homeb2);
    Serial.println("pararmotorbrazo35:");
    Serial.println(pararmotorbrazo35);
    Serial.println("pararmotorbrazo32:");
    Serial.println(pararmotorbrazo32);
    Serial.println("pararmotorz_sup:");
    Serial.println(pararmotorz_sup);
    Serial.println("pararmotorz_inf:");
    Serial.println(pararmotorz_inf);
    //cine=1;
    if (movehome == 1) {
      cine = 1;
      tita1G = 0.0;
      tita2G = 0.0;
      Zpaso = 0.0;
      goto pruebahome;
      //movehome=0;
    }
    vueltacine:
    delay(500);
    home_z();
    delay(500);
    pararmotorz_sup = false;
    homeb1 = false;
    delay(500);
    homeb2 = false;
    home_base();  // rutina de home de la base
    //Serial.println("homeb1: ");
    //Serial.println(homeb1);
    //Serial.println("homeb2: ");
    //Serial.println(homeb2);

    /*delay(500);
      homeb1=false;
      delay(500);
      homeb2=false;*/
    home_brazo();
    delay(500);
    pararmotorbrazo35 = false;
    delay(500);
    pararmotorbrazo32 = false;

    delay(500);
    pararmotorz_inf = false;
    Serial.println("Salida:");
    Serial.println("Homeb1:");
    Serial.println(homeb1);
    Serial.println("Homeb12:");
    Serial.println(homeb2);
    Serial.println("pararmotorbrazo35:");
    Serial.println(pararmotorbrazo35);
    Serial.println("pararmotorbrazo32:");
    Serial.println(pararmotorbrazo32);
    Serial.println("pararmotorz_sup:");
    Serial.println(pararmotorz_sup);
    Serial.println("pararmotorz_inf:");
    Serial.println(pararmotorz_inf);
    tita1pasos_anterior = 0;
    tita2pasos_anterior = 0;
    z_pasos_anterior = 0;
    tita1G = 0;
    tita2G = 0;
    Z = 0;
    /*if (homeb1==1){
        homeb1=false;
        homeb1=0;
        Serial.println("entro");
      }*/

    //Serial.println("homeb1 sal if: ");
    //Serial.println(homeb1);
    /*for(m=0; m<1000; m++){
        digitalWrite(step_3, HIGH);
        delayMicroseconds(700);
        digitalWrite(step_3, LOW);
        delayMicroseconds(700);
      }*/
    //val_menu=0;
  }
  //Serial.println("Salio del for");
  //Serial.println("Sum_angulos:");
  //Serial.println(sum_angulos);
 /* if (input == 'p' ) || sum_angulos > 1) {
    digitalWrite(dir_4, HIGH);
    if (sum_angulos == 1) {
      angulos(-80, 175, 0);
    }
    if (sum_angulos == 1) {
      angulos(-80, 175, -53);
      sum_angulos=0;
    }*/
  
   if ((input == 'p' ) || (input =='o')) {
    digitalWrite(dir_4, HIGH);
    if (input=='p') {
      angulos(-80, 175, 0);
    }
    if (input=='o') {
      angulos(-80, 175, -53);
      sum_angulos=0;
    }

    /*Serial.println(mensaje1);
    while(Serial.available()==0){

    }
    X=Serial.parseInt();
    limpiarBufferSerial();
    Serial.print(mensaje3);
    Serial.println(X);

    Serial.println(mensaje2);
    while(Serial.available()==0){

    }
    Y=Serial.parseInt();
    limpiarBufferSerial();
    Serial.print(mensaje4);
    Serial.println(Y);
    
    Serial.println(mensajez);
    while(Serial.available()==0){

    }
    Z=Serial.parseInt();
    limpiarBufferSerial();
    Serial.print(mensajez_ing);
    Serial.println(Z);


    
    angulos(X,Y);*/
    Serial.println("Valor de tita2G:");
    Serial.println(tita2G);
    Serial.println("Valor de tita1G:");
    Serial.println(tita1G);
    pruebahome:
    digitalWrite(EN, LOW);
    digitalWrite(dir, LOW);
    digitalWrite(EN_3, LOW);
    digitalWrite(dir_3, LOW);  //Motor base sentido antihorario ERA HIGH
    digitalWrite(EN_2, LOW);
    digitalWrite(dir_2, HIGH);  //Motor brazo 2 sentido horario ERA HIGH
    digitalWrite(EN_4, LOW);
    //digitalWrite(dir_4, HIGH); //Con HIGH Sube ERA HIGH
    //pruebahome:
    tita1G_actual = round(tita1G / 0.1125) * 3.16;  //0.1125 porque trabajo con micropasos, 3.16 por la relacion de transformacion entre las poleas
    tita1G_a_pasos = tita1G_actual - tita1pasos_anterior;
    Serial.println("Cantidad de pasos Base");
    Serial.println(tita1G_a_pasos);
    //Serial.println("Cantidad de pasos Base relativo");
    //Serial.println(tita1G_a_pasos);
    if (tita1G_a_pasos < 0) {
      tita1G_a_pasos = -1 * tita1G_a_pasos;
      digitalWrite(dir_3, HIGH);
    }
    /*for(float pasos_base_M3=0.0; pasos_base_M3<tita1G_a_pasos; pasos_base_M3++){////////////////////////// for base
      //digitalWrite(step, HIGH);
      digitalWrite(step_3, HIGH);
      //digitalWrite(step_2, HIGH);
      //digitalWrite(step_4, HIGH);
      delay(temp);
      //digitalWrite(step,LOW);
      digitalWrite(step_3,LOW);
     //digitalWrite(step_2,LOW);
      //digitalWrite(step_4,LOW);
      delay(temp);
    }*/
    tita2G_actual = round(tita2G / 0.1125) * 3.16;  //0.1125 porque trabajo con micropasos, 3.16 por la relacion de transformacion entre las poleas
    tita2G_a_pasos = tita2G_actual - tita2pasos_anterior;
    if (tita2G_a_pasos < 0) {
      tita2G_a_pasos = -1 * tita2G_a_pasos;
      digitalWrite(dir_2, LOW);
    }
    //tita2G_a_pasos=tita2G_a_pasos-tita2G_a_pasos;
    /*
     if (tita2G_a_pasos<0){
     tita2G_a_pasos=-1*tita2G_a_pasos;
     digitalWrite(dir_2, LOW);
    }*/
    Serial.println("Cantidad de pasos Brazo 2");
    Serial.println(tita2G_a_pasos);
    /*for(float pasos_brazo2_M2=0.0; pasos_brazo2_M2<tita2G_a_pasos; pasos_brazo2_M2++){//////////////////// for brazo
      //digitalWrite(step, HIGH);
      //digitalWrite(step_3, HIGH);
      digitalWrite(step_2, HIGH);
      //digitalWrite(step_4, HIGH);
      delay(temp);
      //digitalWrite(step,LOW);
      //digitalWrite(step_3,LOW);
      digitalWrite(step_2,LOW);
      //digitalWrite(step_4,LOW);
      delay(temp);
    }*/
    //MODIFICACION DE Zpaso ABAJO
    /*
    z_actual=Z*(1600/8);//1600 porque esta configurado con micropasos 1/8, 8 porque son 8mm por vuelta de la varilla roscada
    Zpaso=z_actual-z_pasos_anterior;
    if (Zpaso<0){
      Zpaso=-1*Zpaso;
      digitalWrite(dir_4, LOW);//Low baja
   }
   Serial.println("Cantidad de pasos Varilla: ");
    Serial.println(Zpaso);*/
    //MODIFICACION DE Zpaso ARRIBA
    Serial.println("Cantidad de pasos Varilla: ");
    Serial.println(Zpaso);
    /*for(float pasos_varilla=0.0;pasos_varilla<Zpaso;pasos_varilla++){//////////////////////// for varilla
     //digitalWrite(step, HIGH);
      //digitalWrite(step_3, HIGH);
      //digitalWrite(step_2, HIGH);
      digitalWrite(step_4, HIGH);
      delay(temp);
     //digitalWrite(step,LOW);
     //digitalWrite(step_3,LOW);
     //digitalWrite(step_2,LOW);
      digitalWrite(step_4,LOW);
      delay(temp);
    }*/
    ///////////////////////////////////////////////////////////////////////////////
    /*paso_max=tita1G_a_pasos;
    if(tita2G_a_pasos>paso_max){
      paso_max=tita2G_a_pasos;
    } else if(Zpaso>tita2G_a_pasos){
      paso_max=Zpaso;
    }*/
    if (tita1G_a_pasos >= tita2G_a_pasos && tita1G_a_pasos >= Zpaso) {
      paso_max = tita1G_a_pasos;
    } else if (tita2G_a_pasos >= tita1G_a_pasos && tita2G_a_pasos >= Zpaso) {
      paso_max = tita2G_a_pasos;
    } else {
      paso_max = Zpaso;
    }
    Serial.println("El mayor es: ");
    Serial.println(paso_max);

    /*
    Serial.println("Pasos de la base: ");
    Serial.println(tita1G_a_pasos);
    Serial.println("Pasos del brazo: ");
    Serial.println(tita2G_a_pasos);
    Serial.println("Paso de la varilla: ");
    Serial.println(Zpaso);
    Serial.println("El paso mayor es: ");
    Serial.println(paso_max);
    temp_base= ((paso_max*2*temp)/tita1G_a_pasos)/2;
   temp_brazo= ((paso_max*2*temp)/tita2G_a_pasos)/2;
    temp_varilla= ((paso_max*2*temp)/Zpaso)/2;
    Serial.println("Tiempo de la base: ");
    Serial.println(temp_base);
   Serial.println("Tiempo del brazo: ");
    Serial.println(temp_brazo);
    Serial.println("Tiempo de la varilla: ");
    Serial.println(temp_varilla);*/
    //Relaciones
    /*
    Serial.println("Relacion Base-Varilla: ");
    rel_base=Zpaso/tita1G_a_pasos;
    Serial.println(rel_base);
   Serial.println("Relacion Brazo-Varilla: ");
    rel_brazo=Zpaso/tita2G_a_pasos;
   Serial.println(rel_brazo);
   Serial.println("Relacion Varilla-Varilla: ");
    rel_varilla=Zpaso/Zpaso;
    Serial.println(rel_varilla);*/
    /*
    for(int j=0;j<10000;j++){
      cont1++;

     if(abs(fmod(cont1,1.1901928)-0.48)<0.52){
        cont2++;
      }/*
     if(cont3<tita2G_a_pasos){
      if(abs(fmod(cont1,4.1806020)-1.64)<0.52){
        cont3++;
      }
      }*/
    /*
      if(cont3<tita2G_a_pasos){
       if(abs(fmod(cont1,Zpaso/tita2G_a_pasos)-fmod(10,Zpaso/tita2G_a_pasos))<0.52){
       cont3++;
      }
      }

    }*/
    /*
    Serial.println("Contador base ultimo: ");
    Serial.println(cont2);
    Serial.println("Contador brazo ultimo: ");
    Serial.println(cont3);*/
    /*
    Serial.println("modulo: ");
    Serial.println((round(fmod(100,4.18)*1000))/1000);
    Serial.println("modulo: ");
    Serial.println(fmod(100,4.18));*/
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

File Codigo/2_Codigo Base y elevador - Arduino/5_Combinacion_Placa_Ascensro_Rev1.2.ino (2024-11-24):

//Motor Placa
#define STEP_PIN A6
#define DIR_PIN A7
#define ENABLE_PIN A2
#define ENDSTOP_PIN 3 
//Motor ascensor
#define STEP_PIN_1 26
#define DIR_PIN_1 28
#define ENABLE_PIN_1 24
#define ENDSTOP_PIN_1 2
//Variables motor placa
char input;
const int stepsPerRevolution = 400;
const int stepsBack = 98; // Pasos a girar en sentido antihorario cuando se activa el final de carrera
const int stepsForward = 300;
int stepaux;
volatile bool endstopTriggered = false; // Bandera para indicar si el final de carrera ha sido activado
volatile bool motorRunning = false;
//Variables motor ascensor
const int stepsPerRevolution_2 = 200; // Ajusta esto según tu motor
volatile bool endstopTriggered_2 = false; // Bandera para el final de carrera
volatile bool motorRunning_2 = false;

void setup() {
  // Configurar los pines
  pinMode(STEP_PIN, OUTPUT);
  pinMode(DIR_PIN, OUTPUT);
  pinMode(ENABLE_PIN, OUTPUT);
  pinMode(ENDSTOP_PIN, INPUT_PULLUP); // Final de carrera como entrada con pull-up interno

  pinMode(STEP_PIN_1, OUTPUT);
  pinMode(DIR_PIN_1, OUTPUT);
  pinMode(ENABLE_PIN_1, OUTPUT);
  pinMode(ENDSTOP_PIN_1, INPUT_PULLUP); // Final de carrera como entrada con resistencia pull-up

  // Iniciar la comunicación serial
  Serial.begin(9600);
  digitalWrite(ENABLE_PIN_1, LOW); // LOW habilita el motor
  
  
  Serial.println("Presiona 'w' para girar 200 pasos en sentido horario.");
  Serial.println("Presiona 'l' para girar 200 pasos en sentido antihorario.");
  // Habilitar el driver
  digitalWrite(ENABLE_PIN, LOW);

  Serial.println("Escribe 'g' para empezar a girar en sentido horario hasta que se active el final de carrera.");

  // Configurar la interrupción para el final de carrera
  attachInterrupt(digitalPinToInterrupt(ENDSTOP_PIN), endstopInterrupt, FALLING);
  //pinMode(ENDSTOP_PIN_1, INPUT_PULLUP);
  attachInterrupt(digitalPinToInterrupt(ENDSTOP_PIN_1), endstopInterrupt_1, FALLING);
}
void loop() {
  // Comprobar la entrada serial
  if (Serial.available()) {
    char input = Serial.read();

    // Girar en sentido horario al presionar 'g'
    if (input == 'g') {
      Serial.println("Girando en sentido horario...");
      motorRunning = true;
      stepaux=stepsBack;
      rotateUntilEndstop(true, 'g');  // Inicia el giro en sentido horario
    }
    else if (input == 's') {
      Serial.println("Girando 200 pasos en sentido horario...");
      motorRunning = true;
      stepaux=stepsForward;
      rotateUntilEndstop(true, 's');
      //rotateSteps(true, stepsForward); // Girar 200 pasos en sentido horario
      //motorRunning = false;            // Detener el motor
    }
    //else if (endstopTriggered_2) {
      //Serial.println("Final de carrera ya no está activo. Habilitando motor.");
      //endstopTriggered_2 = false;  // Reiniciamos la bandera
      //digitalWrite(ENABLE_PIN_1, LOW); // Rehabilitamos el motor
    //}

    // Girar en sentido horario (200 pasos) al presionar 'w'
    else if (input == 'w') {
      Serial.println("Girando 200 pasos en sentido horario...");
      endstopTriggered_2 = false;
      rotateSteps_2(650, true); // 200 pasos en sentido horario
    }

    // Girar en sentido antihorario (200 pasos) al presionar 's'
    else if (input == 'l') {
      Serial.println("endstopTriggered_2");
      Serial.println(endstopTriggered_2);
      /*if (endstopTriggered_2){
        //endstopTriggered_2 = false;
        rotateSteps_2(5, true);
      }else {
        motorRunning_2 = true;
        endstopTriggered_2 = false;
        //endstopTriggered_2 = false;
        rotateUntilEndstop(true, 'l');
      }*/
      motorRunning_2 = true;
      endstopTriggered_2 = false;
      //endstopTriggered_2 = false;
      rotateUntilEndstop(true, 'l');
      endstopTriggered_2 = false;
      //rotateSteps_2(5, true);
      //Serial.println("ingresaste l");
      //motorRunning_2 = true;//
      //endstopTriggered_2 = false;//
      //endstopTriggered_2 = false;
      //rotateUntilEndstop(true, 'l');//
      //Serial.println("Pasa");
      //delay(5);
      //endstopTriggered_2 = false;  
      
    }
  }

if (endstopTriggered) {
  //Serial.println("Final de carrera activado. Girando 120 pasos en sentido antihorario...");
  rotateSteps(false, stepaux);
        
      //rotateSteps(false, stepsBack); //letra g
      //rotateSteps(false, stepsForward); // letra s
                // Girar 120 pasos en sentido antihorario
  endstopTriggered = false;       // Resetear la bandera
  motorRunning = false;           // Detener el motor
  }
}



// Función para girar el motor hasta que se active el final de carrera
void rotateUntilEndstop(bool clockwise, char n) {
  if (n == 'g' || n == 's'){
    if (clockwise) {
      digitalWrite(DIR_PIN, HIGH); // Sentido horario
    } else {
      digitalWrite(DIR_PIN, LOW);  // Sentido antihorario
    }
    while (!endstopTriggered && motorRunning) {
      stepMotor();   // Gira el motor continuamente
      delay(1);
    }
  }
  else if (n == 'l'){
    digitalWrite(DIR_PIN_1, LOW);//gira antihorario
    //Serial.println(endstopTriggered_2);
    //Serial.println(motorRunning_2);
    while (!endstopTriggered_2 && motorRunning_2) {
      stepMotor_1();   // Gira el motor continuamente
      delay(1);
    }
    motorRunning_2 = false;
  }

}

// Función para girar el motor un número específico de pasos
void rotateSteps(bool clockwise, int steps) {
  if (clockwise) {
    digitalWrite(DIR_PIN, HIGH); // Sentido horario
  } else {
    digitalWrite(DIR_PIN, LOW);  // Sentido antihorario
  }

  for (int i = 0; i < steps; i++) {
    stepMotor();
    delay(1);
  }
}

// Función para un solo paso del motor
void stepMotor() {
  digitalWrite(STEP_PIN, HIGH);
  delayMicroseconds(3000);
  digitalWrite(STEP_PIN, LOW);
  delayMicroseconds(3000);
}

// Función de interrupción del final de carrera
void endstopInterrupt() {
  endstopTriggered = true;  // Activar la bandera cuando el final de carrera se activa
}



// Función para girar un número específico de pasos
void rotateSteps_2(int steps, bool clockwise) {
  Serial.println("ingreso a rotateSteps_2");
  // Configurar la dirección
  digitalWrite(DIR_PIN_1, clockwise ? HIGH : LOW);
  endstopTriggered_2 = false;
  for (int i = 0; i < steps; i++) {
    /*if (endstopTriggered_2) {
      Serial.println(endstopTriggered_2);
      Serial.println("Final de carrera activado. Motor detenido.");
      return; // Detener el motor si el final de carrera está activado
    }*/
    stepMotor_1();
    delay(1); // Ajustar la velocidad del motor
  }
}

void stepMotor_1() {
  digitalWrite(STEP_PIN_1, HIGH);
  delayMicroseconds(3000); // Ajusta este valor para controlar la velocidad
  digitalWrite(STEP_PIN_1, LOW);
  delayMicroseconds(3000); // Ajusta este valor para controlar la velocidad
}

// Función de interrupción del final de carrera
void endstopInterrupt_1() {
  endstopTriggered_2 = true;
  //digitalWrite(ENABLE_PIN_1, HIGH); // Deshabilitar el motor cuando se activa el final de carrera
}
